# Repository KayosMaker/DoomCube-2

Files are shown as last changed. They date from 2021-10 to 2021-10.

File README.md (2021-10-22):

DOOMCUBE
# Doom-Cube
A mod for Voron 2.4; designed by the Voron community, for the Voron community! Please note that it is a work in progress, design iterations are expected. The files are hosted on github so we have a log of the past history for the parts.



#### Key features:

- 4040 vertical components to allow for insulation with air gap stock

- Top mounted Z drives

- Top mounted low voltage components

- Bottom mounted high voltage components

#### Optional

- Replace X/Y cable chains with umbelical (Z chain retained for A/B motors and Y endstop)

#### Changes required:

- 4pcs 4040 extrusions (HFSB5-4040)   -or-   4pcs 404020 rounded extrusions (HFSR5-404020)

- New Z Idlers  (only printed parts required)

- Relocate X/Y endstops  (only printed parts required)

- Cable Glands for Umbelical

#### Tips for printing parts:

For any Voron stock parts, or the Z idlers, please use standard Voron settings.

For skirts, etc, you may use other settings to reduce filament usage. Currently I am using: 0.3mm layer height, 2 perimeters, 2 bottom, 3 top, 20% infill. 

## BOM 

All extrusions are listed using Misumi part numbers.

Part numbers are listed for both square 4040, and rounded 404020 vertical extrusions.  Choose only one type.  The first set of part numbers is for plain cut extrusions.  The second part number is for square extrusions that are cut and drilled by misumi.  

#### Note:
If you choose to use rounded corners, you will need to reuse your frame's existing 2020 vertical extrusions, or purchase a set of them for a scratch build.  The rounded verticals do not require machining, but the 2020 verticals that nest into them will need to have holes drilled to enable securing the rounded piece with blind joints, as shown here.



## Extrusions Based on Standard V2 Build Sizes

## DOOM-350
### Frame Extrusions
#### DIY
Misumi Part #  |Qty
|:----:|:----:|
Square Verticals: HFSB5-4040-530 |4 
Rounded Verticals: HFSR5-404020-530 |4

#### Pre-Drilled
Misumi Part #  |Qty
|:----:|:----:|
Square Verticals: HFSB5-4040-530-LCP-RCP |4

### Door Extrusions

#### DIY
Misumi Part #  |Qty
|:----:|:----:|
HFSB5-2020-530|2
HFSB5-2020-428|2

#### Pre-Drilled
Misumi Part #  |Qty
|:----:|:----:|
HFSB5-2020-530-AH10-BH520|2
HFSB5-2020-428-TPW|2

## DOOM-300
### Frame Extrusions
#### DIY
Misumi Part #  |Qty
|:----:|:----:|
Square Verticals: HFSB5-4040-480 |4
Rounded Verticals: HFSR5-404020-480 |4

#### Pre-Drilled
Misumi Part #  |Qty
|:----:|:----:|
Verticals: HFSB5-4040-480-LCP-RCP |4

### Door Extrusions
#### DIY
Misumi Part #  |Qty
|:----:|:----:|
HFSB5-2020-480|2
HFSB5-2020-378|2

#### Pre-Drilled
Misumi Part #  |Qty|
|:----:|:----:|
HFSB5-2020-480-AH10-BH470|2
HFSB5-2020-378-TPW|2

## DOOM-250
### Frame Extrusions
#### DIY
Misumi Part #  |Qty
|:----:|:----:|
Square Verticals: HFSB5-4040-430 |4
Rounded Verticals: HFSR5-404020-430 |4

#### Pre-Drilled
Misumi Part #  |Qty|
|:----:|:----:|
Square Verticals: HFSB5-4040-430-LCP-RCP| 4

### Door Extrusions

#### DIY
Misumi Part #  |Qty| 
|:----:|:----:|
HFSB5-2020-430|2
HFSB5-2020-328|2

#### Pre-Drilled

Misumi Part #  |Qty| 
|:----:|:----:|
HFSB5-2020-430-AH10-BH420|2
HFSB5-2020-328-TPW|2

## Door Hinges
Silver and Black are listed 

|Misumi Part #  |Qty|Color
|:---:|:---:|:---:|
HHPSN5-SET|2| Silver
HHPBSN5-SET|2| Black

# Ongoing and Future Development
While we all have many irons in the fire, Doomcube v2 is still being worked on.  Keep an eye out for changes coming to the panel printed parts, as well as some coming mods from the community.  In the interest of encouraging more Doom builds, as well as more mods, a complete DOOM CAD file is now available with all the Doom and Voron components together.  Find it in the CAD folder with all the individual component CAD files.  The individual components have been gone through and all hole sizes have been made consistent.  Missing chamfers were added, and some geometry cleaned up.  The frame and panel assemblies will stay as they are until new files are ready.
### CAD Notes
If you examine the complete CAD file you will see it is not limited to the basic DOOM and Voron components.  Included are two optional gantry variants, with a handful of popular community produced V2 mods installed.  The file is structured to be very easy to see what you want, and hide what you don't.  The step file has everything shown by default, so you'll need to hide the frame, skirts, and gantries you don't wish to see.  It should only take a few clicks.

DoomCubing is a great way to improve your v2.  It's also a perfect time to install several mods, while you have things partially disassembled.  To give you some ideas about possible mod combos, the optional modded gantries in the complete cad file contain the following excellent mods:

### Afterburner MGN12 Gantry
Mod|Repository
|:---:|:---:|
Ark's MGN12|https://github.com/VoronDesign/VoronUsers/tree/master/printer_mods/arkeet/mgn12
Hartk's GE5C Spherical Z Joint|https://github.com/hartk1213/MISC/tree/main/Voron%20Mods/Voron%202/2.4/Voron2.4_GE5C
Hartk's Pinmod (X/Y Joints, ,A/B Drive Frames, A/B idlers, Z idlers)|https://github.com/hartk1213/MISC/tree/main/Voron%20Mods/Voron%202/2.4/Voron2.4_Pins_Mod

### Mantis MGN12 Gantry
Mod|Repository
|:---:|:---:|
Long's Mantis Toolhead|https://github.com/VoronDesign/VoronUsers/tree/master/printer_mods/Long/Mantis_Dual_5015
Hartk's GE5C Spherical Z Joint|https://github.com/hartk1213/MISC/tree/main/Voron%20Mods/Voron%202/2.4/Voron2.4_GE5C
Hartk's Pinmod (X/Y Joints,A/B Drive Frames, Z idlers)|https://github.com/hartk1213/MISC/tree/main/Voron%20Mods/Voron%202/2.4/Voron2.4_Pins_Mod
Phalanx's Other Idlers|https://github.com/selliott79/Other-V2-Idlers

### Other Mods
The following mods are present in all or most Doomcube variants in the complete CAD file.  Klicky is not on the Mantis toolhead, since it has a native magprobe that works identically to Klicky.

Mod|Repository
|:---:|:---:|
L.e.o.p.a.r.d and Hartk's Sexbolt Z Endstop|https://github.com/hartk1213/MISC/tree/main/Voron%20Mods/Voron%202/2.4/Voron2.4_SexBolt_ZEndstop
josar's Klicky Probe|https://github.com/jlas1/Klicky-Probe 
whoppingpochard's Gantry Rail Backers|https://github.com/tanaes/whopping_Voron_mods/tree/main/extrusion_backers

#### A big thanks to all original authors for permission to include their mods in the Doomcube CAD!  Always follow the links to their respective repos for the latest stl's, and info on how to best make use of their mods.

##### A set of stl checklists to match these mod sets is in the works.  That can be one of the most confusing parts of building up a modded printer from scratch, or doing many mods at once with redundant components.  Hopefully a few checklists will simplify things a little bit.  A huge debt is owed to all the mod makers and their willingness to share their work!  Keep up the good work y'all!

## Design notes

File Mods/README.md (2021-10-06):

# Mods

Printer mods for DOOMCUBE
Remember to update this README when uploading new mod!

## Table structure

Update the following table with the information about your mod:
- Your name
- A link to your sub-folder
- A short description of your mod

like so:
`
| Creator | [Mod title](link) | Description |`

---

| Creator | Mod title | Description |
| --- | --- | --- |
| crag-h4k | [direct drive z](./crag-h4k/direct-drive-z) |Replaces z motor assembly with a minimized direct drive z motor unit. |
| crag-h4k | [galileo adxl345 chain replacement](./crag-h4k/galileo-adxl345-chain-replacement) |Replaces the Galileo extruders's chain mount with a dedicated mount for a adxl345. |
| crag-h4k | [lil a drive cable cover](./crag-h4k/lil-a-drive-cable-cover) | Replaces beefy a-drive cable cover with a cute little cover - use with top mounted cable gland. |
| crag-h4k | [mgn12 galileo compatible cable gland mount](./crag-h4k/mgn12-galileo-cable-gland) | Simple cable gland mount for mgn12 x-axis mod and Galileo extruder. |
| crag-h4k | [z chain m12 gland ptfe anchor](./crag-h4k/z-chain-cable-gland-ptfe-anchor) | Simple a cable gland mount and 4mm PTFE tube pass-through for upper Z chain anchor - attempts to preserve z-axis build volume.  |
| mvieleers | [My Custom DoomCube-2](./mvieleers/my_doomcube) | 300m3 DoomCube-2 with several popular included and a few of my own mods. |
| mvieleers | [Schaffner FN-286 Plug Panel](./mvieleers/fn-286_plug_panel) | Modded Plug Panel to hold the Schafnner FN-286|
| mvieleers | [Corner Panel Mounts](./mvieleers/corner_panel_mounts)| Modded upper and lower corner caps and square feet to attach the top and bottom deck panels to the feet with magnets. |
| mvieleers | [Galileo ADXL345 Chain Replacement with Umbilical Mount](./mvieleers/adxl_mount_w_umbilical)| This mod is an alteration of crag-h4k's mod to replace the chain mount on a Galileo extruder with an adxl345 mount. The adxl345 mount has cutouts so an umbilical can be mounted to the adxl345 mount with tie-wraps.
| KayosMaker | [tip-in swing-in panels](./KayosMaker/Toolless%20Panel%20Mod) | Work In Progress - nothing now, just a frame generator and some shaved corner pieces.  will post the rest soon |

---

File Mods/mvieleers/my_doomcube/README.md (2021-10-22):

# DoomCube
Based on the DoomCube Mod for the Voron V2 and several popular Mods out there, I decided to capture my personalized DoomCube build in a full CAD.

This repository will list any Mods used that deviate from the regular Voron V2.4 and DoomCube build.

Different types of Mods are used in this build:
- Personal DoomCube modifications. These are the deviations from the original DoomCube files. **Please note: the modifications are specific to this particular build which is a 300m3 build. Be very carefull if you use these files and make sure they can be applied to your situation.** The files will be hosted under this "My DoomCube" Mod. You can find the files under [STL](STL)
- Official Mods. These are official Mods for the Voron V2.4 and DoomCube and are untouched by me and implemented as is. I will link to their official github where you will need to download the files relevant for you.
- Altered DoomCube specific Mods. These are Mods by me based on the official DoomCube files and applicable to any DoomCube build. They will be hosted seperately under the [Mods section of the official DoomCube repository](../..). You will need to download the files from their own mod repository.
- Voron V2 Mods by me. These are Mods by me that are applicable to any Voron V2 (Doomed or not) and will be hosted from my [own Github](https://github.com/mvieleers/Voron-V2) where you can download the files.

**If I don't specify a part, it means that you will need to download the STL from the [Original DoomCube repository](https://github.com/FrankenVoron/DoomCube-2), or in case the part is not listed there as well, from the original [Voron 2 repository](https://github.com/VoronDesign/Voron-2).**

[Make sure to join the DoomCube discord!](https://discord.gg/EAANfEk25f)

## CAD
A full CAD for this build will is available. For the most part it will include fasteners as well, with the exception for flanges, skirts and panelmounts.
As the CAD is 100 Mb+ it cannot be uploaded as one into Github. I've broken it up in different sections (one of these also needed to be zipped). When you import the STEP files into a new drawing, it will form one complete assembly again.

Click [HERE](CAD) for STEP files

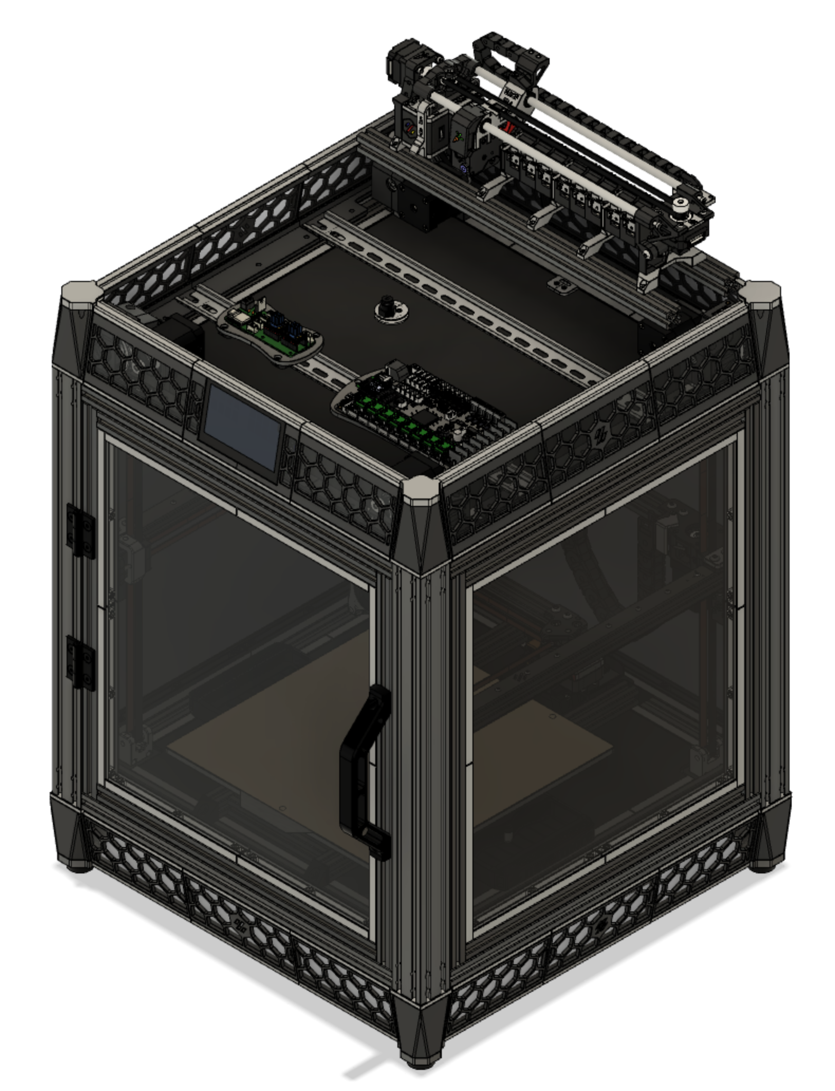
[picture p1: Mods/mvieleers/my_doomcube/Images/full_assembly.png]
Full Assembly


## Frame

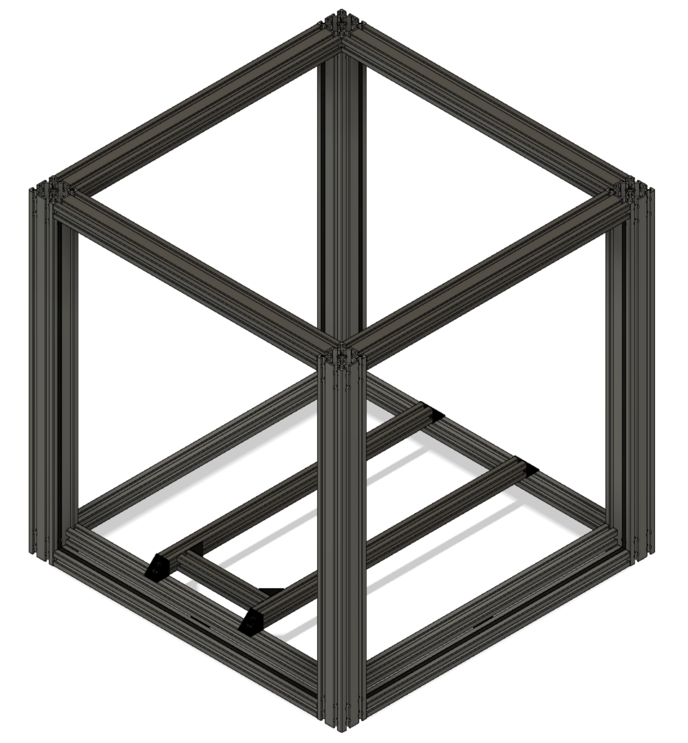
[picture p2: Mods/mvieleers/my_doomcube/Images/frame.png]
Frame


### Specifics
- 300m3 build.
- I'm using 20mm taller vertical 4040s, so the door, side and back panels all rest within an extrusion frame. This eliminates the need for the flanges to support the panels.
- Instead of 2020's for the top frame, I'm using 4020's.
- Instead of single 2020's for the bottom frame, I'm using double 2020's in the bottom frame in order for the panels to rest on top of the additional 2020 extrusion.
- The bed frame has a cross bar in order to mount my bed with 3 mounting points instead of 4. It is a preparation to add a kinematic bed mounting solution at a later time.
- I'm using slot covers to seal any gaps between the frame and the side panels. The slot covers are also intended to keep the panel in place. In order for this to work the slot cover need to protrude above the extrusion. Misumi HSCKS5 slot covers will not work for this goal as they sit completely flush with the extrusion. I've found that Aliexpress slot covers work well for this.
- The CAD shows slot covers on all 4 sides of the frame where the panel is placed. If you actually use slot covers on all 4 sides, you will have the best seal of any gaps, but removing the panel later will require a lot of force. I've found that using slot covers on 3 sides works best. It still makes a good seal and you'll be able to fairly easy push the entire panel out when you require them of for maintenance or printing pla.

### Hardware
Section|Part| Part #|QTY|Remarks
|:---:|:----:|:----:|:---:|:---:|
Bottom Frame
||Bottom Horizontals|[HFSB5-2020-420-TPW](https://uk.misumi-ec.com/vona2/detail/110302683830/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)|8|Can be reused if you're converting from a standard V2 300
||OpenBuilds Angle Corner Connector|[20x20x20](https://openbuildspartstore.com/black-angle-corner-connector/)|4|Used to keep the two extrusions from rotating
||Slot Covers|[DCR6-2020](https://nl.aliexpress.com/item/1005001664501395.html?spm=a2g0s.9042311.0.0.27424c4dtVOEhL)|1m|Comes in 10m so needs to be cut to length.
Vertical Frame
||Square Verticals|[HFSB5-4040-500-LWP-RWP-TPW](https://uk.misumi-ec.com/vona2/detail/110302684530/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)|4
||Slot Covers|[DCR6-2020](https://nl.aliexpress.com/item/1005001664501395.html?spm=a2g0s.9042311.0.0.27424c4dtVOEhL)|2m|Comes in 10m so needs to be cut to length.
Top Frame
||Top Horizontals|[HFSB5-2040-420-TPW](https://uk.misumi-ec.com/vona2/detail/110302684350/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)|4
||Slot Covers|[DCR6-2020](https://nl.aliexpress.com/item/1005001664501395.html?spm=a2g0s.9042311.0.0.27424c4dtVOEhL)|1m|Comes in 10m so needs to be cut to length.
Bed Frame
|||[HFSB5-2020-420-TPW](https://uk.misumi-ec.com/vona2/detail/110302683830/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)|2|Can be reused if you're converting from a standard V2 300
|||[HFSB5-2020-130](https://uk.misumi-ec.com/vona2/detail/110302683830/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)|1
||OpenBuilds Angle Corner Connector|[20x20x20](https://openbuildspartstore.com/black-angle-corner-connector/)|6|4 for securing the bed frame to the bottom frame, 2 to secure the cross bar. 4 can be reused if you're converting from a standard V2

## Panels

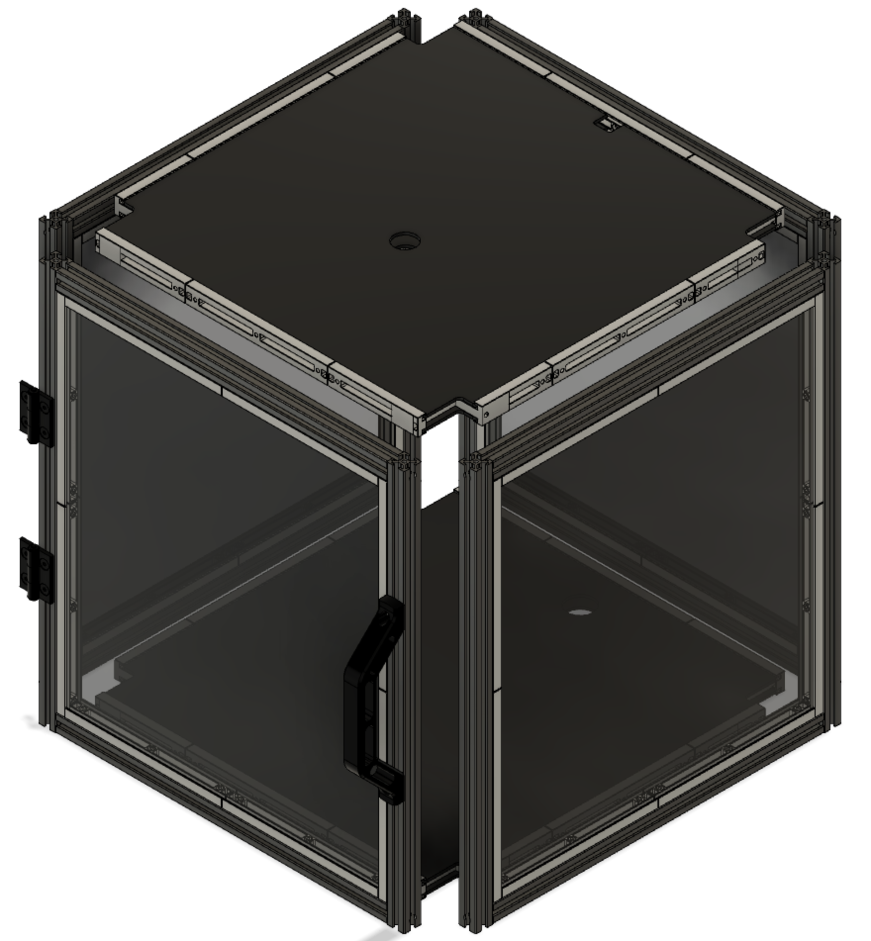
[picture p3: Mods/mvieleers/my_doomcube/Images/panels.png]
Panels


### Specifics
- The principle of the original DoomCube door is applied to the side and back panels, where the panels slide into panelmounts that bolt into the extrusion. This method is copied to all the sides. For my 300 build I went with 2 pieces per extrusion though. Please check whether you can fit these on your build plate if printing this on a small printer.
- The slot covers (see frame section) should create a good seal and a tight fit, which should make the panels to securely stay in place. If this is not the case, I have modded the excellent [Annex Engineers Panel Clips for 2020 extrusions](https://github.com/Annex-Engineering/Annex-Engineering_Other_Printer_Mods/tree/master/All_Printers/Annex_Panel_2020_Clips_and_Hinges/panel_clips_and_corners). The Mod involves flattening the clips so it sits flush with the side panel frame. Please take note of the [Annex Engineering EULA](STL/Panels/Panel%20Clips/LICENSE.md)
It looks like the misumi slot covers might sit too flat in the extrusion. Aliexpress slot covers stick out more and might make a better fit. Will provide final results when I finish the build.
- Top and bottom panels use the "standard" Doomcube panelmounts, but the corners have been modded to include the part that goes in between the panels (from [Kayosmaker's mod](https://github.com/FrankenVoron/DoomCube-2/tree/main/Mods/KayosMaker/Toolless%20Panel%20Mod/Panel%20Frame%20Generator%20WORK%20IN%20PROGRESS). This should add to the stability.
- Top and bottom (deck) panels have cutouts for wire passthroughs and the top deck panel has mounting holes for mounting the ERCF on top of the top deck panel.

### Dimensions
Drawings are [here](Drawings), DXFs are [here](DXF)

Panel|Drawing|DXF|QTY
|:---:|:---:|:---:|:---:|
Door|panel_side.pdf|panel_side.dxf|2
Sides|panel_side.pdf|panel_side.dxf|4
Back|panel_back.pdf|panel_side.dxf|2
Top|panel_top.pdf|panel_top.dxf|2
Bottom|panel_bottom.pdf|panel_bottom.dxf|2
Top Deck|panel_top_deck.pdf|panel_top_deck.dxf|1
Bottom Deck|panel_bottom_deck.pdf|panel_bottom_deck.dxf|1

### Printed Parts
Section|Part|STL Origin|QTY
|:---:|:---:|:---:|:---:|
Door / Side / Back Panel Mounts
|Horizontal piece|[This Mod](STL/Panels/Sides)|16
|Vertical piece|[This Mod](STL/Panels/Sides)|16
|Corner Panel Clips|[This Mod](STL/Panels/Panel%20Clips)|16 (optional)
|Center Panel Clips|[This Mod](STL/Panels/Panel%20Clips)|16 (optional)
|Key for Corner and Center Panel Clips|[Annex Engineering Offical](https://github.com/Annex-Engineering/Annex-Engineering_Other_Printer_Mods/blob/master/All_Printers/Annex_Panel_2020_Clips_and_Hinges/panel_clips_and_corners/key/STL/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)|36 (optional)
Top / Bottom Panel
|Straight center piece|[This Mod](STL/Panels/Top_Bottom)|8
|Corner piece 1|[This Mod](STL/Panels/Top_Bottom)|4
|Corner piece 2|[This Mod](STL/Panels/Top_Bottom)|4
|Corner piece 1 mirrored|[This Mod](STL/Panels/Top_Bottom)|4
|Corner piece 2 mirrored|[This Mod](STL/Panels/Top_Bottom)|4

### Hardware
Hardware|Part|QTY|Remarks
|:---:|:---:|:---:|:---:
Vertical extrusions|[HFSB5-2020-458-LCH-RCH](https://uk.misumi-ec.com/vona2/detail/110302683830/?HissuCode=HFSB5-2020-458-LCH-RCH)|8
Horizontal extrusions|[HFSB5-2020-378-TPW](https://uk.misumi-ec.com/vona2/detail/110302683830/?HissuCode=HFSB5-2020-378-TPW)|8
Handle|[Aluminum Alloy Door Handle](https://nl.aliexpress.com/item/1407596513.html?spm=a2g0s.9042311.0.0.66fb4c4deTZEmA)|1|CAD shows printed door handle, I use this type of aluminum handle in size 120mm (ordered without screws and nuts)
Hinge|[HHPBSN5-SET](https://uk.misumi-ec.com/vona2/detail/110302362010/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)|2

## Skirts

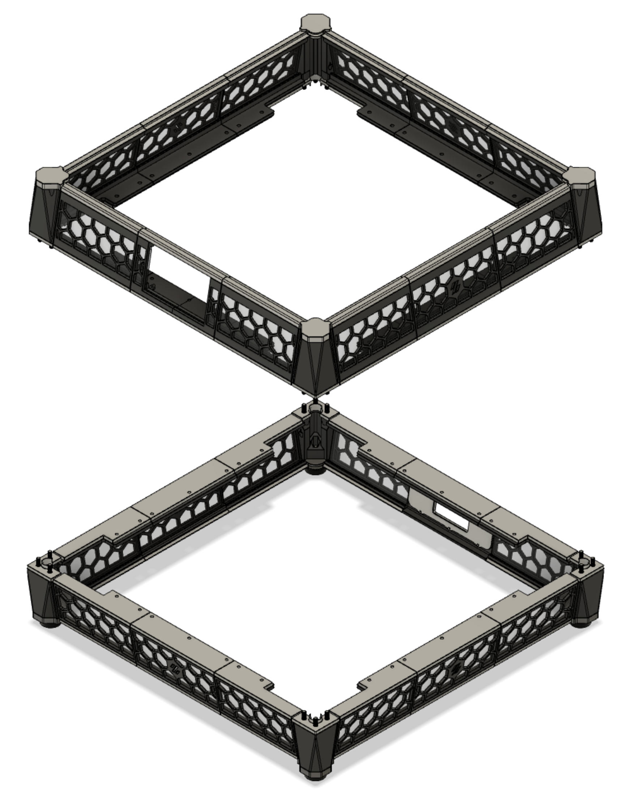
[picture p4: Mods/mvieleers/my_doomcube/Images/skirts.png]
Skirts


### Specifics
- Basis is the hexagon skirts from the original DoomCube. 
- Due to side and back panel mounting system, flanges of the door are used all around as well as the panelmounts.
- Panelmounts are 2 pieces per side, instead of 3. This might not be printable on smaller bed sizes.
- Top and Bottom have altered top caps for the corners. These caps allow the deck panels to be attached to the corners with magnets.
- Top corners and skirts have been increased in size in order to accomodate my Waveshare 4,3" LCD. For this a center skirt was modded to hold the LCD.

### Dimensions
Drawings are [here](Drawings), DXFs are [here](DXF)

Panel|Drawing|DXF|QTY
|:---:|:---:|:---:|:---:|
Bottom Center Skirt Panel|skirt_bottom_center.pdf|skirt_bottom_center.dxf|3
Bottom Side Skirt Panel|skirt_bottom_side.pdf|skirt_bottom_side.dxf|8
Top Center Skirt Panel|skirt_top_center.pdf|skirt_top_center.dxf|3
Top Side Skirt Panel|skirt_top_side.pdf|skirt_top_side.dxf|8
Top LCD Skirt Panel|skirt_top_lcd.pdf|skirt_top_lcd.dxf|2

### Printed Parts
Section|Part|STL Origin|QTY
|:---:|:---:|:---:|:---:|
Square Corners Foot
||Bottom Corner|[Corner Panel Mounts](../corner_panel_mounts/STL)|4
||Top Corner|[This Mod](STL/Skirts/Corners/Top)|4
||Foot Mount (to extrusion)|[Original](../../../STLs/Corners/Square%20Extrusions)|8
||Bottom Corner Cap (panel mount)|[Corner Panel Mounts](../corner_panel_mounts/STL)|4
||Top Corner Cap (panel mount)|[This Mod](STL/Skirts/Corners/Top)|4
Skirts
||Bottom Center Skirt|[Original](https://github.com/FrankenVoron/DoomCube-2/tree/main/STLs/Skirts/Hexagon%20Skirts)|3
||Bottom Left Side Skirt|[Original](https://github.com/FrankenVoron/DoomCube-2/tree/main/STLs/Skirts/Hexagon%20Skirts/300)|4
||Bottom Right Side Skirt|[Original](https://github.com/FrankenVoron/DoomCube-2/tree/main/STLs/Skirts/Hexagon%20Skirts/300)|4
||Bottom Power Inlet Skirt|[Original](https://github.com/FrankenVoron/DoomCube-2/tree/main/STLs/Skirts)|1
||Bottom Power Inlet Skirt Inlay|[FN-286 Plug Panel](../fn-286_plug_panel)|1
||Top Center Skirt|[This Mod](STL/Skirts/Skirts/Top)|3
||Top Left Side Skirt|[This Mod](STL/Skirts/Skirts/Top)|4
||Top Right Side Skirt|[This Mod](STL/Skirts/Skirts/Top)|4
||Top LCD Skirt|[This Mod](STL/Skirts/Skirts/Top)|1
Flanges
||Center Flange|[Original DoomCube Door Center Flange](https://github.com/FrankenVoron/DoomCube-2/tree/main/STLs/Door/Flanges)|8
||Side Flange|[Original DoomCube Door Side Flange](https://github.com/FrankenVoron/DoomCube-2/tree/main/STLs/Door/Flanges)|16
Skirt Accents
||Center Skirt Accent|[Original](https://github.com/FrankenVoron/DoomCube-2/tree/main/STLs/Skirts/Hexagon%20Skirts)|7
||Left Side Skirt Accent|[Original](https://github.com/FrankenVoron/DoomCube-2/tree/main/STLs/Skirts/Hexagon%20Skirts/300)|8
||Right Side Skirt Accent|[Original](https://github.com/FrankenVoron/DoomCube-2/tree/main/STLs/Skirts/Hexagon%20Skirts/300)|8

### Hardware
Hardware|Part|QTY|Remarks
|:---:|:---:|:---:|:---:
4.3" LCD|[Waveshare 4.3" LCD DSI](https://www.waveshare.com/4.3inch-dsi-lcd.htm)|1|The Raspberry Pi can be screwed to the LCD screen
Power Inlet|[Schaffner FN-286](https://www.digikey.nl/product-detail/en/schaffner-emc-inc/FN286-1-06/817-1928-ND/1997125?productid=1997125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)|1

## Heated Bed

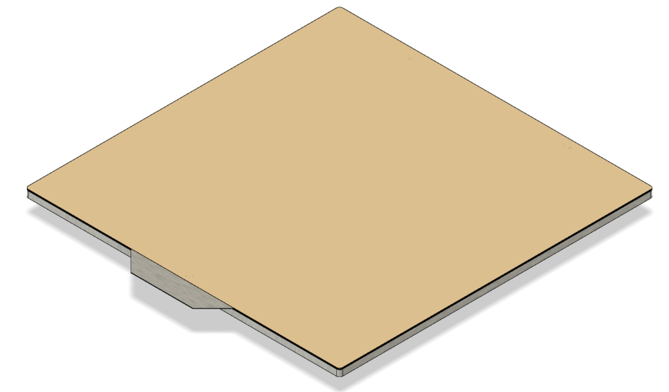
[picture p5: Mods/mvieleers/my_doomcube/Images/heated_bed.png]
Heated Bed


### Specifics
- Mandela Rose Works ultra flat bed is used. It has mounting holes for both the V1.8 and the V2.4. Therefor I'm able to use a triangle 3-point mounting method, by inserting a cross bar between the two bed extrusions. This is also done to accomodate for a kinematic mounting system that is in development with Mandela Rose Works and uses 3 mounting points.
- When not using a kinematic mounting solution, you will only need 3 of the original knurled knuts

### Hardware
Hardware|Part|QTY|Remarks
|:---:|:---:|:---:|:---:
Mic6 Bed|[Mandala Rose Works Ultra Flat Bed](https://www.mandalaroseworks.com/shop/voron/voron-300-standard-bed)|1|
Heater|[Keenovo 240x240 600W 220V](https://keenovo.store/collections/standard-keenovo-silicone-heaters/products/keenovo-square-silicone-heater-3d-printer-build-plate-heatbed-heating-pad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)|1
Magnetic Sheet|[Graviflex 310x310](https://fermio.xyz/en/mechanical/magnetic-sheets/121/magnetic-sheet-310x310x1mm)|1|
Spring Steel Plate|[300x300 Spring Steel Plate](https://www.vonwange.com/product/300x300mm-1-4310-spring-steel-plate/)|1|
PEI Sheet|[Buildtak 12x12" PEI](https://www.buildtak.com/product/buildtak-3d-printing-surface-pei/)|1|
Knurled Nuts|Voron Standard Knurled Nuts|3|

## Z-Assembly

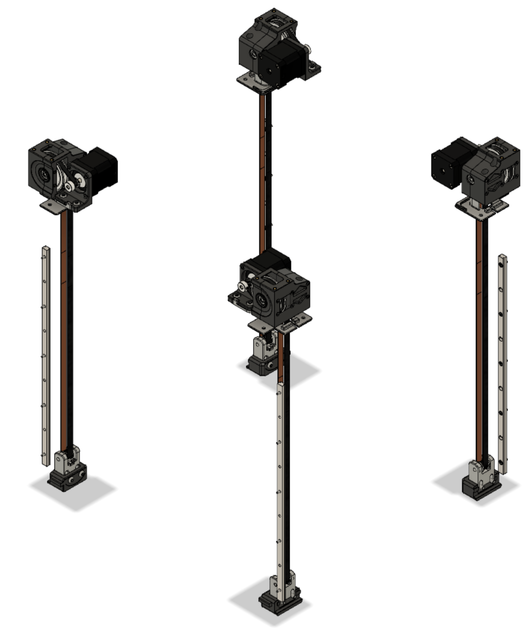
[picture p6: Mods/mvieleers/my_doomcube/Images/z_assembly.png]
Z Assembly


### Specifics
- Z-Drives are completely original DoomCube
- Motor Mounts are taken from the DoomCube CAD, there are no stl's for this in the repository which implies to use the original V2.4 parts. Those have 3 mounting points though, I like the 4 mounting points better, so I created the stl from the DoomCube CAD.
- The belt covers are modded from the original non-reflectix belt covers, I just added a somewhat different ledge to make a tighter integration to the panels.
- I'm using the 9mm pinned Z-Idlers

Section|Part|STL Origin|QTY
|:---:|:---:|:---:|:---:|
Z-Drive
||Z-Drive Main|[Original](https://github.com/FrankenVoron/DoomCube-2/tree/main/STLs/Z_Drives)|2 standard, 2 mirrored
||Z-Drive Retainer|[Original](https://github.com/FrankenVoron/DoomCube-2/tree/main/STLs/Z_Drives)|2 standard, 2 mirrored
Motor Mount
||Motor Mount|[This Mod](STL/Z-Assembly/Z-Drives)|2 standard, 2 mirrored
Z-Idler
||Belt Tensioner 9mm pinned|[Original](https://github.com/mvieleers/DoomCube-2/tree/main/STLs/Z_Idlers)|4
||Tensioner bracket|[Original](https://github.com/mvieleers/DoomCube-2/tree/main/STLs/Z_Idlers)|2 standard, 2 mirrored
Belt Cover
|| Belt Cover|[This Mod](STL/Z-Assembly/Belt%20Covers)|2 standard, 2 mirrored

## Gantry

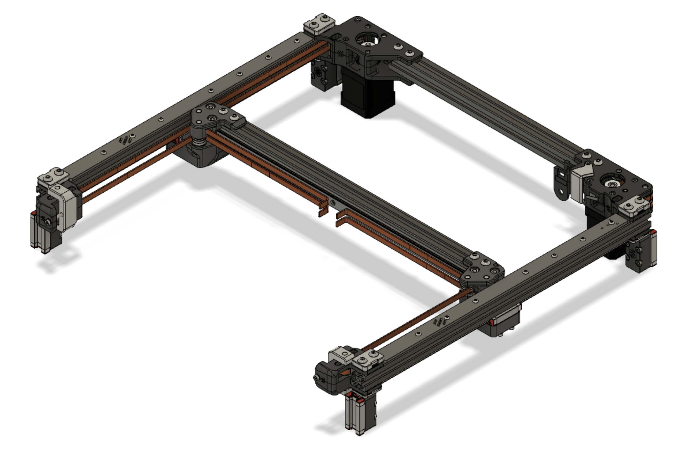
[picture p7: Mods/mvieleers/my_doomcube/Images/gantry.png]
Gantry


### Specifics
The Gantry is a combination of several official Mods. Take good care to select the correct versions from each Mod so they work together.
**Due to using the MGN12 mod in combination with the Gantry Backing Plates Mod and the Y Endstop Relocation Mod, the Y-endstop will trigger to soon due to the added backer. Therefor I've included a modded upper part for the A-drive with the Y endstop mounting point 3mm recessed.**
|Mod|Creator|
|:---:|:---:|
|[MGN12 X axis](https://github.com/VoronDesign/VoronUsers/tree/master/printer_mods/arkeet/mgn12)|arkeet
|[Pins Mod](https://github.com/VoronDesign/VoronUsers/tree/master/printer_mods/hartk1213/Voron2.4_Pins_Mod)|hartk1213
|[Y Endstop Relocation](https://github.com/VoronDesign/VoronUsers/tree/master/printer_mods/hartk1213/Voron2.4_Y_Endstop_Relocation)|hartk1213
|[Upper part A-drive (pinned with Y-endstop 3mm recessed)](STL/Gantry/AB_Drive_Units)|mvieleers
|[GE5C](https://github.com/hartk1213/MISC/tree/main/Voron%20Mods/Voron%202/2.4/Voron2.4_GE5C/STLs)|hartk1213
|[Gantry Backing Plates](https://github.com/VoronDesign/VoronUsers/tree/master/printer_mods/whoppingpochard/extrusion_backers)|whoppingpochard
|[lil a drive cable cover](https://github.com/mvieleers/DoomCube-2/tree/main/Mods/crag-h4k/lil-a-drive-cable-cover)|crag-h4k

### Hardware
There are no deviations from the standard Voron V2 in terms of extrusions.

## X-Carriage

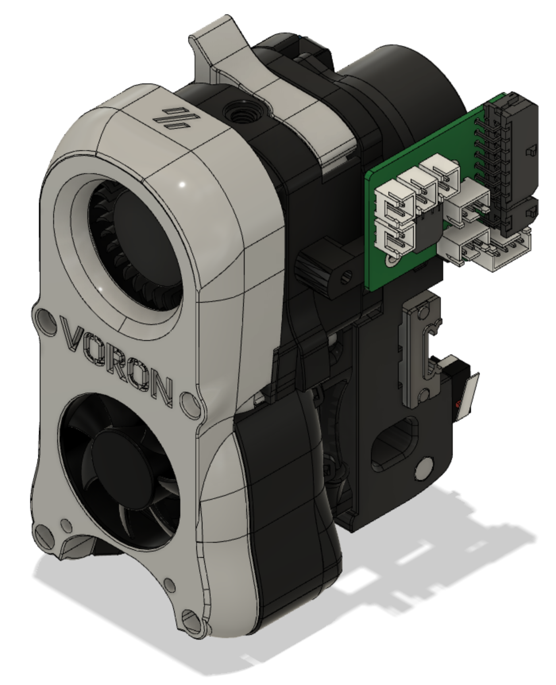
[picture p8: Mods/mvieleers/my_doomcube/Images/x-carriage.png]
X-Carriage


### Specifics
Like the Gantry, the X-Carriage is a combination of several official Mods. Again, take good care to select the correct STL's that work with your setup.
|Mod|Creator|
|:---:|:---:|
|[BlueDragonX's Klicky Mods-Voron 2.4 Direct Mount MGN12 X Carriage](https://github.com/jlas1/Klicky-Probe/tree/main/Usermods/bluedragonx)|bluedragonx
|[Galileo Clockwork](https://github.com/JaredC01/Galileo)|JaredC01
|[AB-BN-30](https://github.com/VoronDesign/VoronUsers/tree/master/printer_mods/Badnoob/AB-BN)|Badnoob
|[Simple mount for Hartk board for galileo.](https://github.com/VoronDesign/VoronUsers/tree/master/printer_mods/Majarspeed/Hartk_Mount_Galileo)|Majarspeed
|[Afterburner Toolhead Board - ERCF version](https://github.com/hartk1213/MISC/tree/main/PCBs/Afterburner_Toolhead_PCB)|hartk1213
[Galileo ADXL345 Chain Replacement with Umbilical Mount](../adxl_mount_w_umbilical)|mvieleers

### Printed Parts
The CAD contains the Galileo Clockwork body. In reality I am using the non-released version of the ERCF 1.1 filament sensor which replaces the Galileo Clockwork body. This STL circulates in the Enraged Rabbit Channel on Discord, but as it is not officially released, I will not provide it in this repository yet. It will be released together with the new ERCF 1.1 version. Please keep an eye out on the official and amazing [Enraged Rabbit Project](https://github.com/EtteGit/EnragedRabbitProject) for more information.
 
### Hardware
I'm using a Mosquito Standard Flow hotend.

## Other

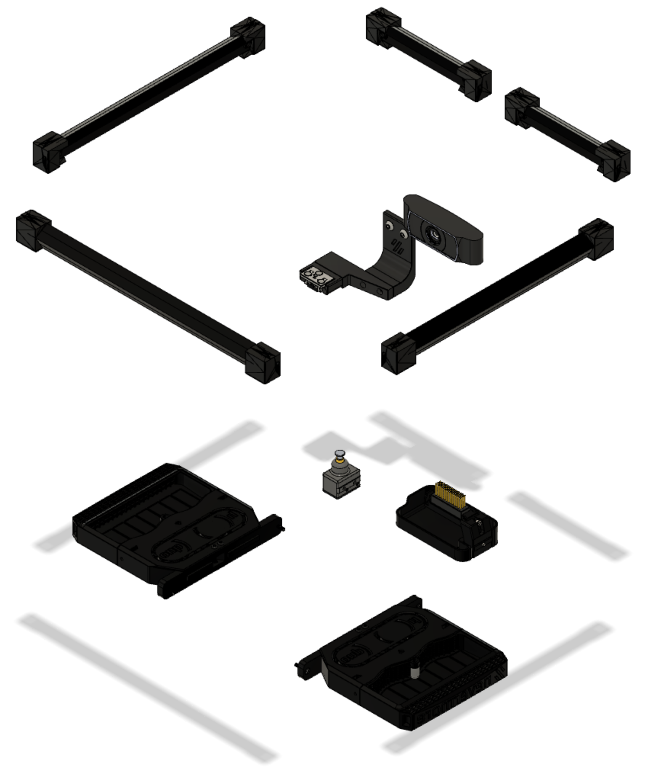
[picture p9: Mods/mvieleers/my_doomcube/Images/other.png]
Other


### Specifics
This section contains several additional Mods to complete the setup within the chamber
|Mod|Creator|
|:---:|:---:|
|[SexBolt Z endstop](https://github.com/hartk1213/MISC/tree/main/Voron%20Mods/Voron%202/2.4/Voron2.4_SexBolt_ZEndstop)|hartk1213
|[Klicky-Probe](https://github.com/jlas1/Klicky-Probe)|jlas1 a.k.a. JosAr
|[Purge brush bucket](https://github.com/Annex-Engineering/Annex-Engineering_Other_Printer_Mods/tree/master/All_Printers/Purge_Brush_Bucket)|Annex Engineering
|[Nevermore Micro V5 Duo](https://github.com/0ndsk4/VoronUsers/tree/0ndsk4/printer_mods/0ndsk4/Nevermore_Air_Filter/Nevermore_Micro)|0ndsk4
|[Angry Led Mount](https://github.com/VoronDesign/VoronUsers/tree/master/printer_mods/42bios/LED_mount)|42bios
|[USB Camera Mount](https://github.com/VoronDesign/VoronUsers/tree/master/printer_mods/Takuya/USBCameraMount)|Takuya

### Hardware
Hardware|Part|QTY|Remarks
|:---:|:---:|:---:|:---:
Led Bar|[LumenTEC LT3 Profile](https://lumentec.eu/Aluminium-Eckig-LED-Profil-100cm-45-fuer-8-12mm-LED-Streifen-Profil-LT3-Abdeckung)|2|
USB Camera|[Wansview 1080p Webcam](https://www.wansview.com/cn/proinfo.aspx?proid=37&categoryid=3&aids=1)|1

## Electronics

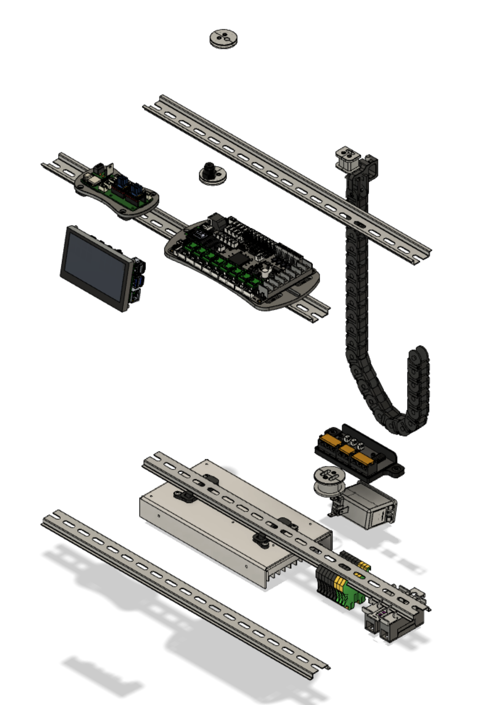
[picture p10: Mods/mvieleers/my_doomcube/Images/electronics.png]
Electronics


### Specifics
- I'm using 5 wire grommets for the passthrough of wires and the reverse bowden tube through the panels. The wire grommets are specific to this build, however the initial idea and credit goes to LoCoCNC's [Wire Grommet Mod](https://github.com/VoronDesign/VoronUsers/tree/master/printer_mods/LoCoCNC/wire_grommets).
  - Wire grommet for passthrough of Tircowns ERCF easy board to the ERCF
  - PTFE grommet for passthrough of PTFE from top deck panel to top panel
  - PTFE and Umbilical grommet for passthrough of PTFE and Wires to the toolhead
  - Wire grommet for the Z-chain wires
  - Wire grommet for the wires trough the bottom panel to the bottom of the chamber
- The Z-chain uses the original Voron V2.4 mounting brackets, they are simply reversed to run it from the top to the A drive
- I'm using a Raspberry Pi 4b, directly attached to the Waveshare 4.3" LCD screen, the BTT Octopus v1.1 and Tircown's ERCF Easy Board. I use TMC 2209 as stepper driver for everything.
- In the chamber, to tidy up the wiring under and behind the heated bed, I'm using a PCB as a central connection point.
- As the standard DoomCube was envisioned, I have my PSU and SSR on the underside and the controller boards in the top compartiment. This way high and low voltage are seperated and you have easy access to the controller boards.
- All electronics in the lower and upper compartment are placed on DIN rails so I never need to change holes in the panels to mount them. The DIN Rails are not screwed to the panel (like on the Voron V2.4, but are attached with screws (on top of the skirts base) to the extrusion.
- I use Phoenix UT 2,5 terminal blocks for wire management, this is optional.

|Mod|Creator|
|:---:|:---:|
[Heated Bed PCB](https://github.com/mvieleers/Voron-V2/tree/main/PCB/Heated%20Bed)|mvieleers
[V2_Octopus_Mount](https://github.com/walttriano/V2_Octopus_Mount)|walttriano
[ERCF Easy Board Mount](https://github.com/Tircown/ERCF-easy-brd/tree/main/mods/DIN%20mount)|mvieleers

### Printed Parts
Part|STL Origin|QTY
|:---:|:---:|:---:|
ERCF Wire Grommet (4 parts)|[This Mod](STL/Electronics/Grommets)
PTFE Wire Grommet(4 parts)|[This Mod](STL/Electronics/Grommets)
PTFE and Umbilical Grommet (4 parts)|[This Mod](STL/Electronics/Grommets)
Z-Chain Grommet (4 parts)|[This Mod](STL/Electronics/Grommets)
Heated Bed Grommet (4 parts)|[This Mod](STL/Electronics/Grommets)

### Hardware
Hardware|Part|QTY|Remarks
|:---:|:---:|:---:|:---:
Controllers
||[Raspberry Pi 4b](https://www.raspberrypi.org/products/raspberry-pi-4-model-b/)|1|
||[BTT Octopus v1.1 with TMC 2209](https://nl.aliexpress.com/item/1005002613363656.html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)|1|
||[Tircown's ERCF Easy Board with TMC 2209](https://github.com/Tircown/ERCF-easy-brd)|1|
4.3" LCD|[Waveshare 4.3" LCD DSI](https://www.waveshare.com/4.3inch-dsi-lcd.htm)|1|The Raspberry Pi can be screwed to the LCD screen
Power Inlet|[Schaffner FN-286](https://www.digikey.nl/product-detail/en/schaffner-emc-inc/FN286-1-06/817-1928-ND/1997125?productid=1997125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)|1
PSU|[Meanwell LRS-200-24](https://www.digikey.nl/product-detail/en/mean-well-usa-inc/LRS-200-24/1866-3332-ND/7705026?productid=7705026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)|1|
SSR|[Omron G3NA](https://industrial.omron.nl/nl/products/G3NA-210B-UTU-5-24VDC)|1|
DIN Mount for SSR|[Omron G3NA DIN Rail Mount](https://nl.rs-online.com/web/p/relay-sockets/8278478/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)|1|
Terminal Blocks|[Phoenix Contact UT2,5](https://www.phoenixcontact.com/online/portal/nl/pxc/product_list_pages/!ut/p/z1/xVTfT9swEP5beMij43PjpOYxVBOIAQN1gyYvke04rVnipI7bAH_9nG0vlSDVhKr5wb6Tvvvul-9wjlc4N3yv1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)|As much as you need|Several accessoires available

## Enraged Rabbit Carrot Feeder

The ERCF is completely stock please refer to the amazing [Enraged Rabbit Project Github](https://github.com/EtteGit/EnragedRabbitProject) by EtteGit.

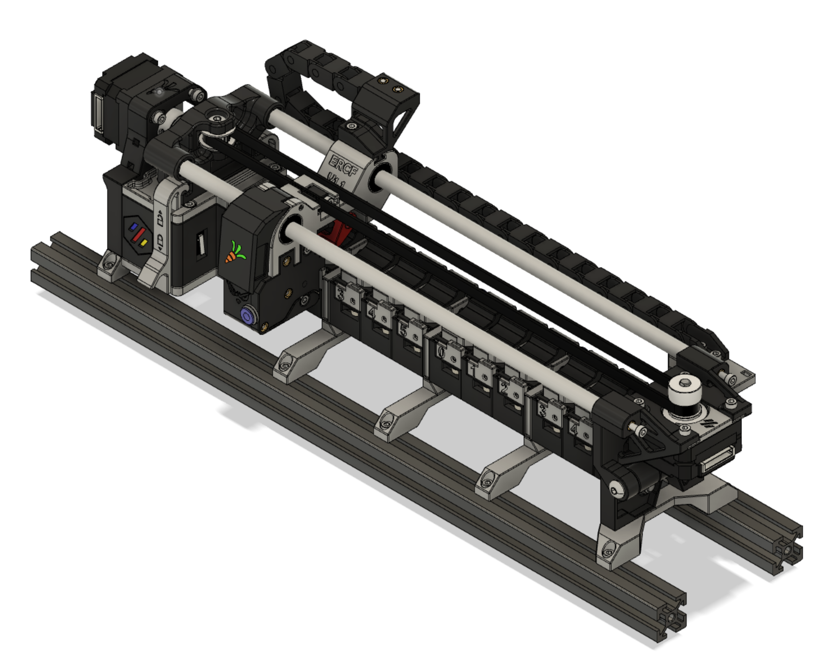
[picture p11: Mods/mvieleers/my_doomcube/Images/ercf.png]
ERCF


### Specifics
 - 12 Channel ERCF. Number of channels is irrelevant as I mount the ERCF to the extrusion and the extrusion is mounted to the top deck panel.

### Hardware
For mounting the frame to the Top Deck Panel you will need the following hardware:

Part|QTY
|:---:|:---:|
|[HFSB-2020-420](https://uk.misumi-ec.com/vona2/detail/110302683830/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)|2
|M5x10 BHCS|6|
|M3x8 SHCS|10|

#### A big thanks to all original creators for all their hard work to create all the Mods that were used in this DoomCube build. Always follow the links to their respective repos for the latest stls, and info on how to best make use of their mods.

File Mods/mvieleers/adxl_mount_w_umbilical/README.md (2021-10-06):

# Galileo ADXL345 Chain Replacement with Umbilical Mount

This mod is an alteration of crag-h4k's mod to replace the chain mount on a Galileo extruder with an adxl345 mount. The original mod can be found [here](https://github.com/FrankenVoron/DoomCube-2/tree/main/Mods/crag-h4k/galileo-adxl345-chain-replacement).

The only thing I did to it, was to add two cutouts that allow two 3mm tie-wraps to be attached to the mount. This can be used to secure an umbilical to the X-carriage.

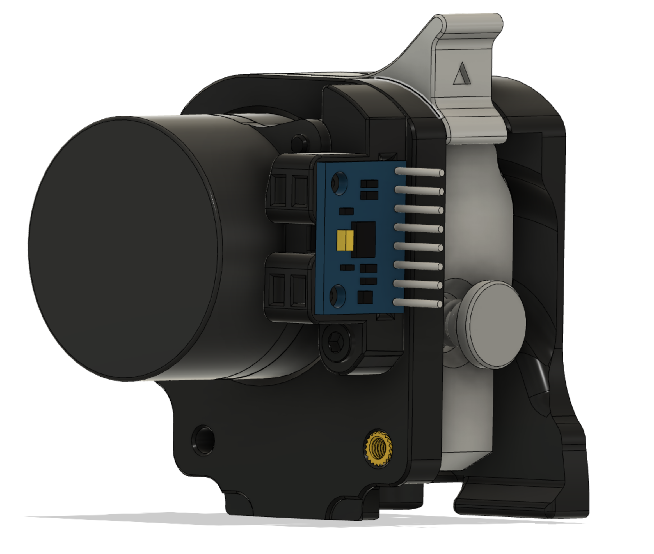
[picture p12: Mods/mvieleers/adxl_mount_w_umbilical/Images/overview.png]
ADXL Mount with Umbilical mount


### Hardware
Part|QTY
:---:|:---:
3x4x5 heatset insert (standard Voron)| 1
3mm tie-wrap|2

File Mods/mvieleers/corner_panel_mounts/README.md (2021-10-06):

# Corner Panel Mounts

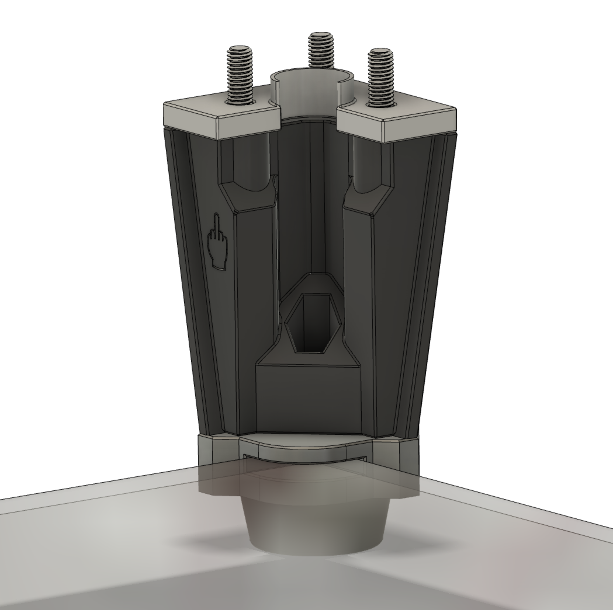
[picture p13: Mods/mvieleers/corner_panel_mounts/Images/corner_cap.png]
Corner Panel Mount

This mod replaces the square feet and the upper and lower corner caps from the original DoomCube.

The feet have been modded so that they each get 2 6x3 round magnets. The corner caps hold 2 magnets as well and they have a slot so they can go around the corners of the top and bottom deck panels. This way the deck panels are magnetically attached to the feet. When a 3mm panel is used, the panels align with the top of the skirts.

The bottom corner cap also has a cutout to hold an m5 hex nut, so the [Misumi Rubber Feet C-30-RK-3215](https://uk.misumi-ec.com/vona2/detail/110500157910/?HissuCode=C-30-RK-3215) can be attached to the corner feet.

### Hardware
Part|QTY
:---:|:---:
6x3mm round magnet (standard Voron)| 32
[Misumi Rubber Feet C-30-RK-3215](https://uk.misumi-ec.com/vona2/detail/110500157910/?HissuCode=C-30-RK-3215)|4

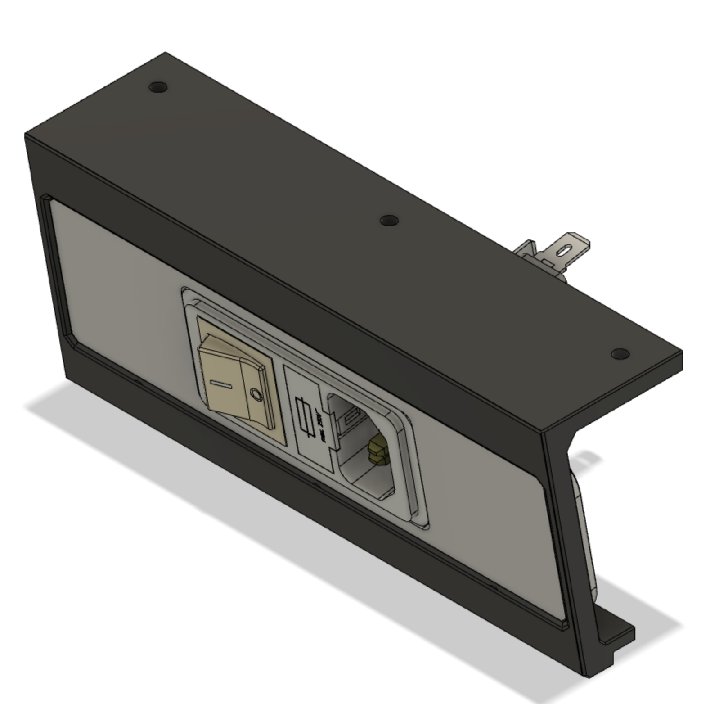
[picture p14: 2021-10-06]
Mods/mvieleers/fn-286_plug_panel/Images/power_panel.png

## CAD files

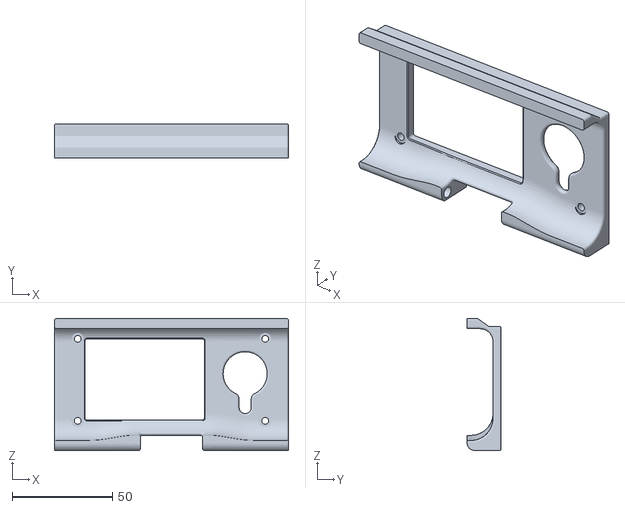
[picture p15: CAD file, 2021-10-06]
Mods/KayosMaker/Top Side LCD for Stock Skirts Semi Doom/lcd panel mirrored adjusted for top side use.stl
117.0 x 17.0 x 66.0

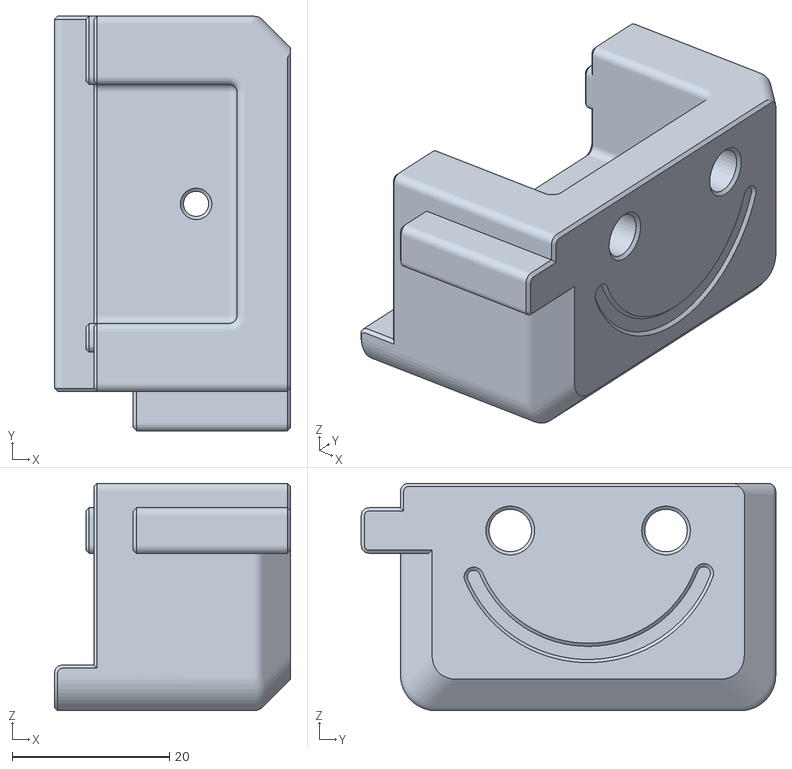
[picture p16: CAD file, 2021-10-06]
Mods/KayosMaker/Z Idlers for Full 4040 Frame/z idler body for 4040 frame.stl
30.0 x 52.7 x 28.9

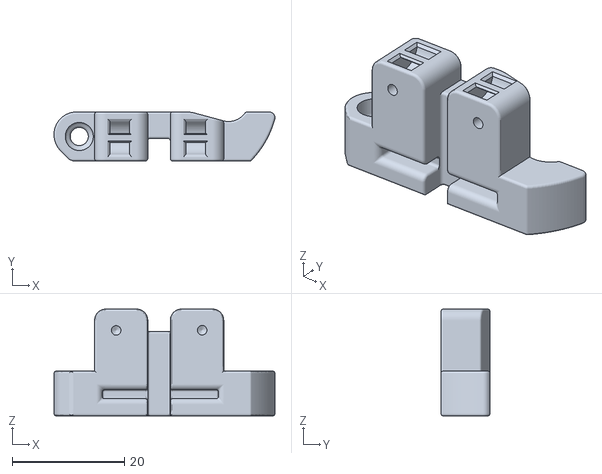
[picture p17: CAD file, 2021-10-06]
Mods/mvieleers/adxl_mount_w_umbilical/STL/adxl mount_w_umbilical_mount.stl
39.3 x 8.72 x 19.0

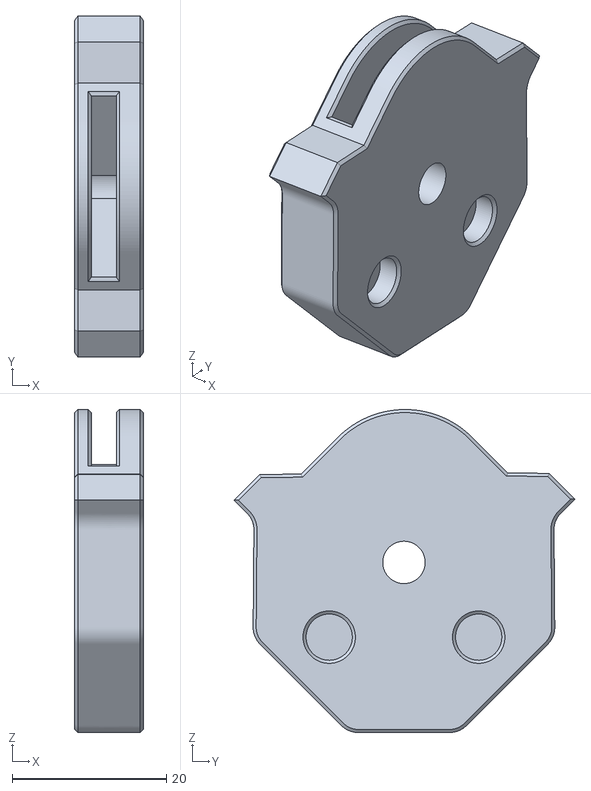
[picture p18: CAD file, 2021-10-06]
Mods/mvieleers/corner_panel_mounts/STL/[a]_bottom_panelmount_x4.stl
8.90 x 44.2 x 41.9

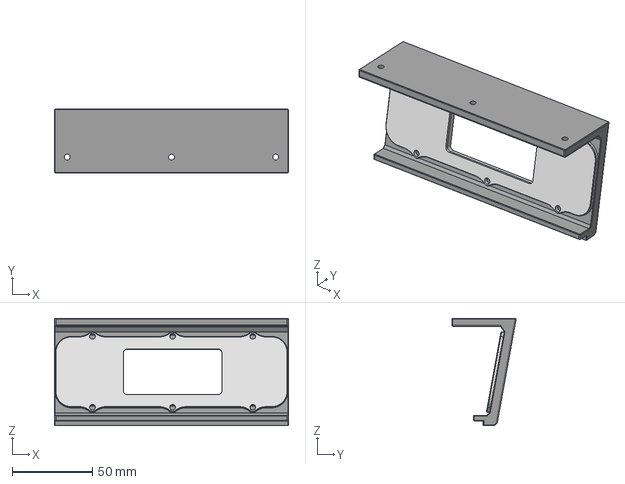
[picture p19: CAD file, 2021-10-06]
Mods/mvieleers/fn-286_plug_panel/CAD/power_panel.step
146.0 x 40.0 x 67.0 mm
(FINAL EDIT) TOP SKIRT BASE PART (SKIRT ELECTRON INSERTION)
plug_panel_filtered_mains_keystone

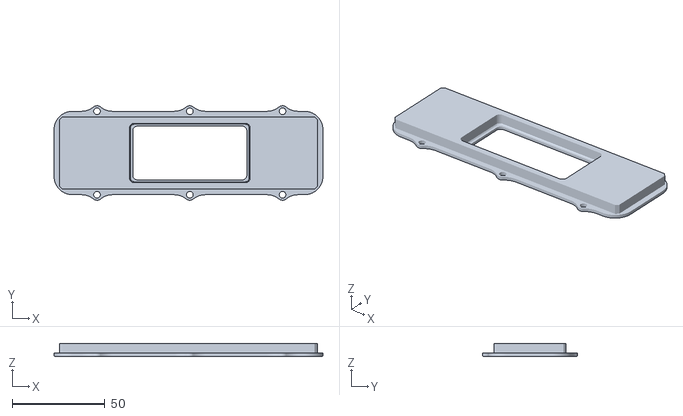
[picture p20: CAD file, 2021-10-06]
Mods/mvieleers/fn-286_plug_panel/STL/[a]_skirt_inlet_accent.stl
145.0 x 51.0 x 7.00

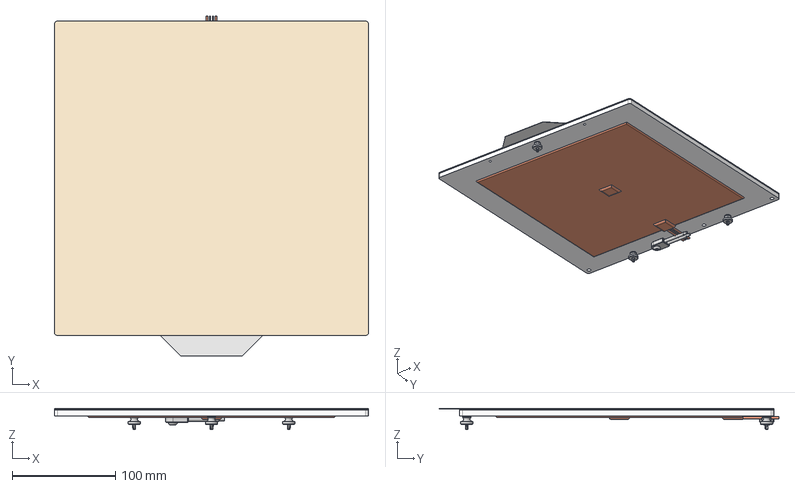
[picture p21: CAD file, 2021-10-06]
Mods/mvieleers/my_doomcube/CAD/heated_bed.step
305.0 x 330.0 x 20.4 mm
BuildTak PEI
Spring Steel Plate 1.4310
GraviFlex Magnetic Sheet
MRW Mic6 Ultra Flat Bed
Heater 240x240
Thermal Fuse
92095A208_Button Head Hex Drive Screw
91292A115
91292A115 (1)
91292A115 (1) (1)

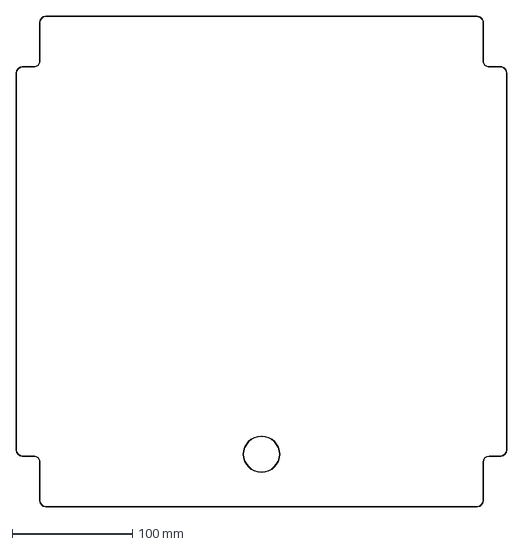
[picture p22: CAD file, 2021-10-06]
Mods/mvieleers/my_doomcube/DXF/panel_bottom.dxf
408.0 x 408.0 mm

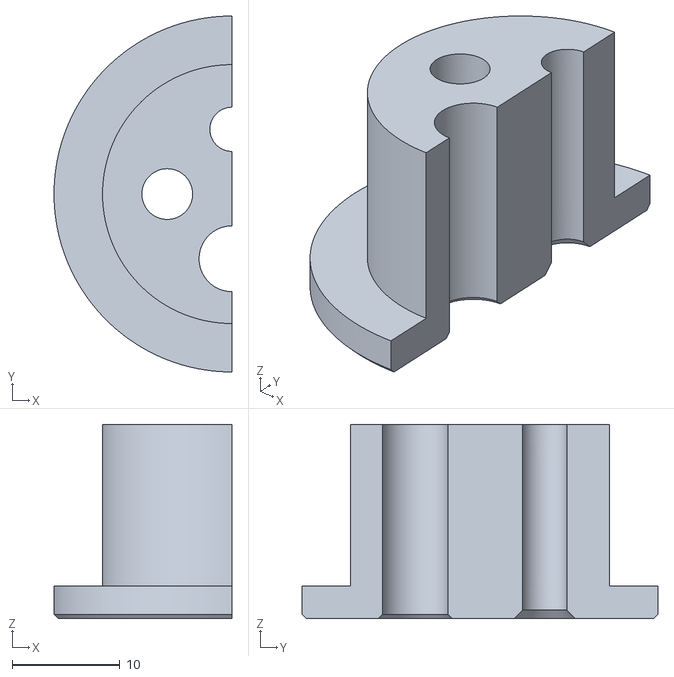
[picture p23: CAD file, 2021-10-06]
Mods/mvieleers/my_doomcube/STL/Electronics/Grommets/[a]_grommet_umbilical_top_b.stl
16.5 x 33.0 x 18.0

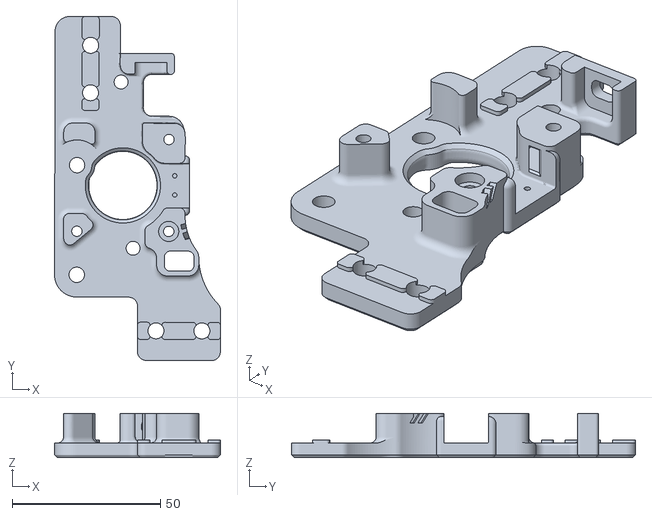
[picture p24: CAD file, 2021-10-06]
Mods/mvieleers/my_doomcube/STL/Gantry/AB_Drive_Units/a_drive_frame_upper_with_jst_y_endstop-3mmback_pinned.stl
56.0 x 116.1 x 15.0

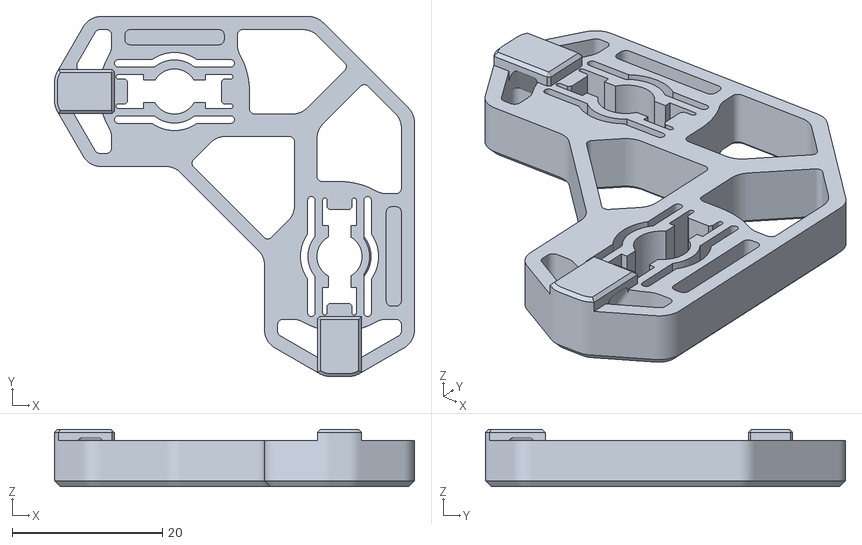
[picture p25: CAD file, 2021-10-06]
Mods/mvieleers/my_doomcube/STL/Panels/Panel Clips/corner_lock_body_flat_x12.stl
48.0 x 48.0 x 7.60

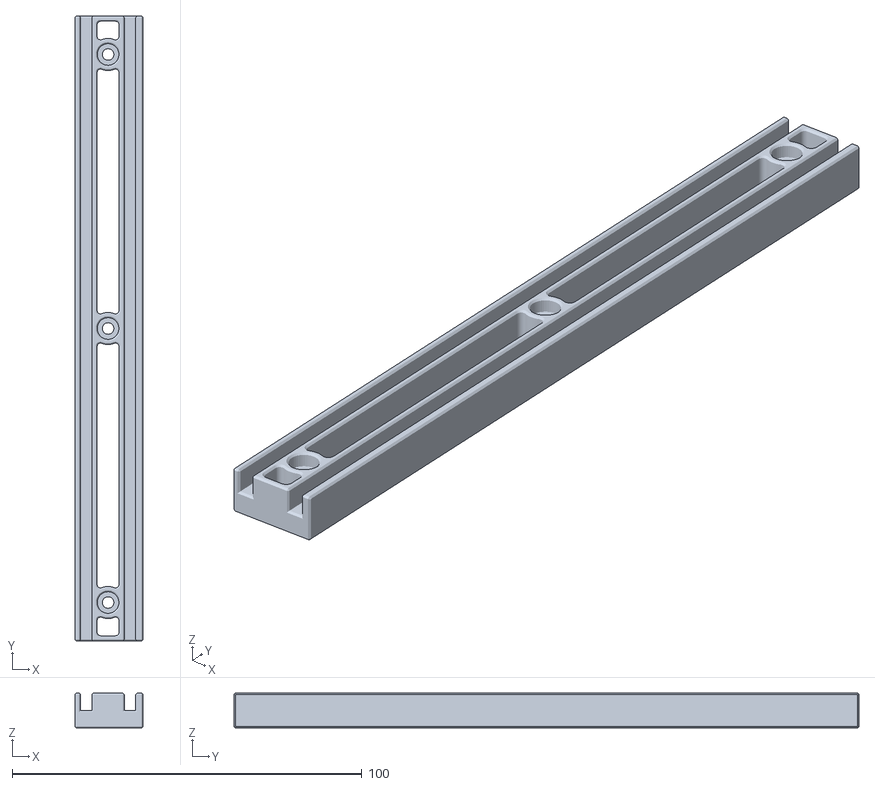
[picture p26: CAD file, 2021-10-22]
Mods/mvieleers/my_doomcube/STL/Panels/Sides/[a]_horizontal_x16.stl
19.5 x 178.8 x 10.0

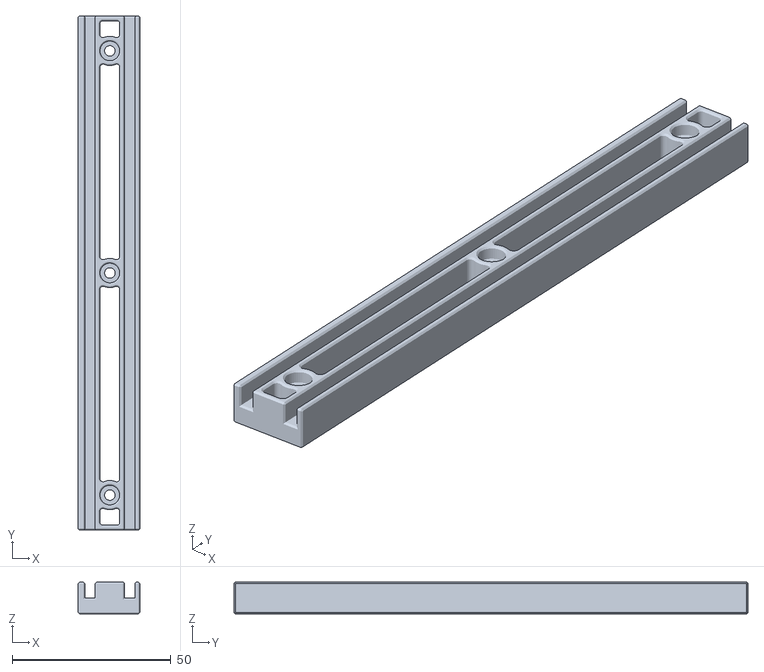
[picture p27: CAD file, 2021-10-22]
Mods/mvieleers/my_doomcube/STL/Panels/Top_Bottom/[a]_center_x8.stl
19.5 x 162.0 x 10.0

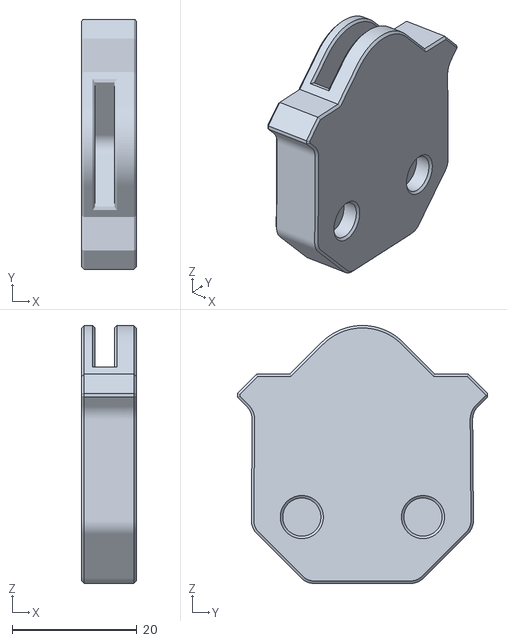
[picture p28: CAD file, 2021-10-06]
Mods/mvieleers/my_doomcube/STL/Skirts/Corners/Top/[a]_top_panelmount_x4.stl
8.75 x 40.0 x 41.3

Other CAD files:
Mods/mvieleers/my_doomcube/STL/Skirts/Skirts/Top/skirt_lcd.stl
Mods/mvieleers/my_doomcube/STL/Z-Assembly/Belt Covers/[a]_a_belt_cover_x2.stl
Mods/mvieleers/my_doomcube/STL/Z-Assembly/Z-Drives/b_motor_mount_x2.stl
STLs/Corners/Rounded Extrusions/Lower/lower_corner_x4.stl
Mods/KayosMaker/Top Side LCD for Stock Skirts Semi Doom/DemiDoom top lcd skirt panel v1.step
Mods/KayosMaker/Z Idlers for Full 4040 Frame/z idler body for 4040 frame mirrored x2.stl
Mods/mvieleers/corner_panel_mounts/STL/[a]_top_panelmount_x4.stl
Mods/mvieleers/corner_panel_mounts/STL/foot_x8.stl
Mods/mvieleers/my_doomcube/DXF/panel_bottom_deck.dxf
Mods/mvieleers/my_doomcube/DXF/panel_side.dxf
Mods/mvieleers/my_doomcube/DXF/panel_top.dxf
Mods/mvieleers/my_doomcube/DXF/panel_top_deck.dxf
Mods/mvieleers/my_doomcube/DXF/skirt_bottom_center.dxf
Mods/mvieleers/my_doomcube/DXF/skirt_bottom_side.dxf
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
